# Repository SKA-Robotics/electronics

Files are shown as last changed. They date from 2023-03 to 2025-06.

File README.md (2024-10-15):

# Electronics
This repository contains documentation of electronic modules used on Sirius 2 Rover.

## How to use this repository
First, clone this repository to your computer.

```bash
$ git clone https://github.com/SKA-Robotics/electronics
```
Open ``SKAR.DsnWrk`` file in Altium designer.
This will load every project into your workspace, allowing you to browse or edit any of them.
When adding a new project, make sure it's part of the project group.

## Maintaining clean and readable documentation

To ensure that everyone can read the documentation, include following files in the final release:
- Datasheets of all important components used
- Any custom libraries containing schematic and layout files
- Schematic **in *.PDF* format**
- Manufacturing data (X2 gerbers)
- Exported 3D model in *.step* format (make sure your stackup has correct thickness set!)
- Images or 3D renders of the both sides
- A short README with description of your board, functionalities, connectors and instructions

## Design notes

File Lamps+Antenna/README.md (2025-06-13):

## Short description
This board contains three parts:
- 24V Step-Up/Step-Down voltage regulator
- LED signal tower controller
- POE injector

## Schematic
The full schematic is available at [schematic.pdf](schematic.pdf)

## Pcb layout
Board dimensions: 100m x 80mm

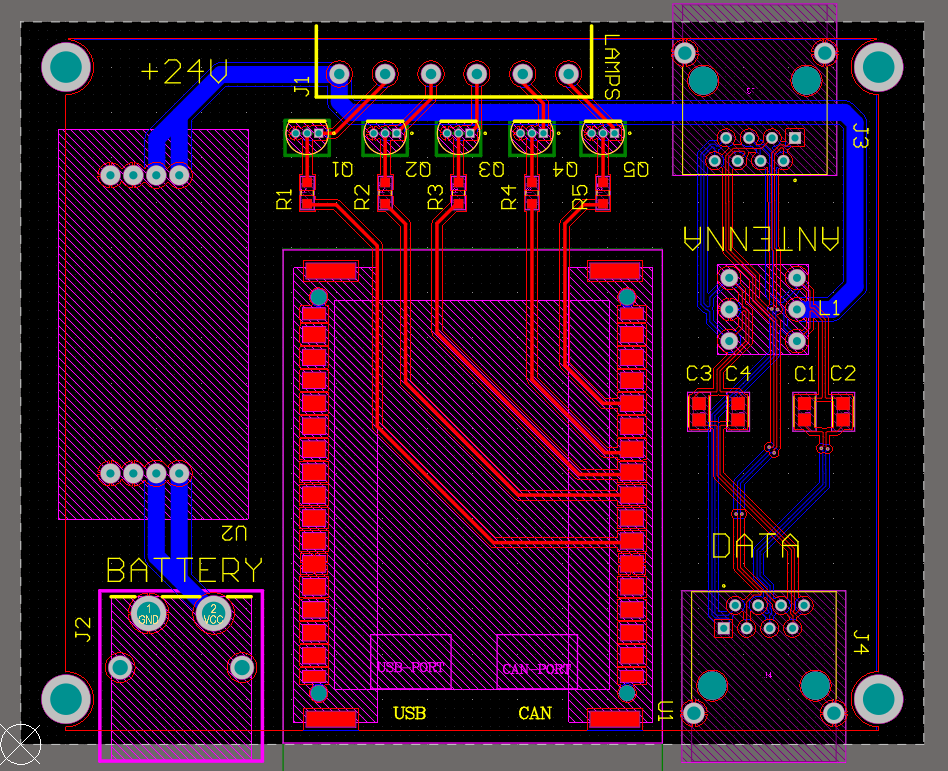
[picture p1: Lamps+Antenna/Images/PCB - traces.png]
PCBTraces


### 3D view
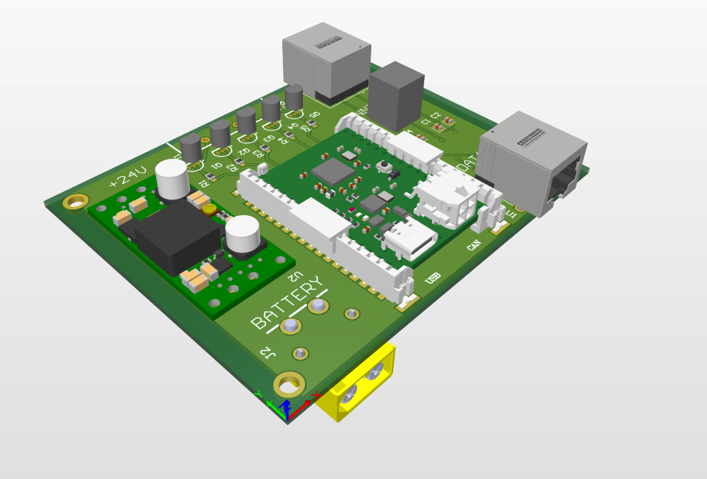
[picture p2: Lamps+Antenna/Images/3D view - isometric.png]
Isometric

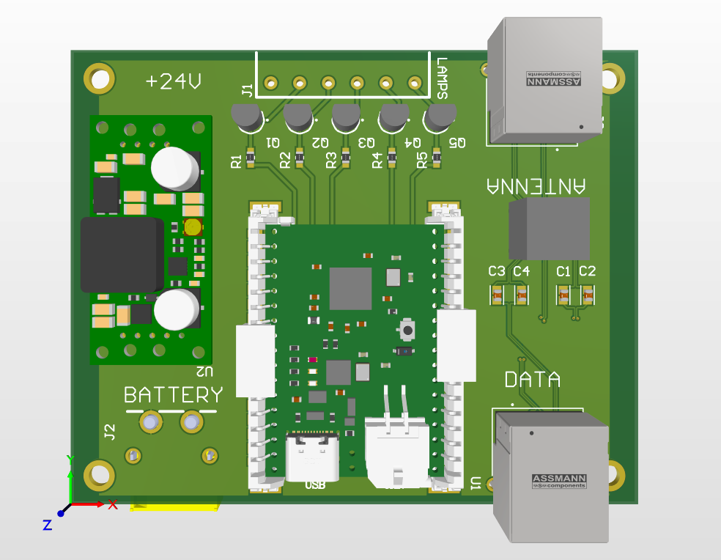
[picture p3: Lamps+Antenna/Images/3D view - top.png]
Top

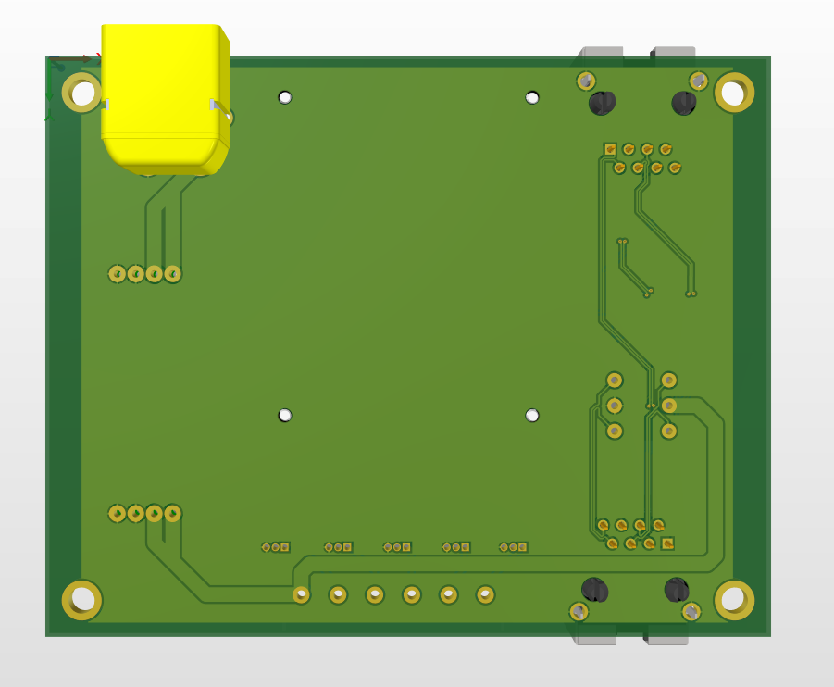
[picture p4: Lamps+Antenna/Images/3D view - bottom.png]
Bottom

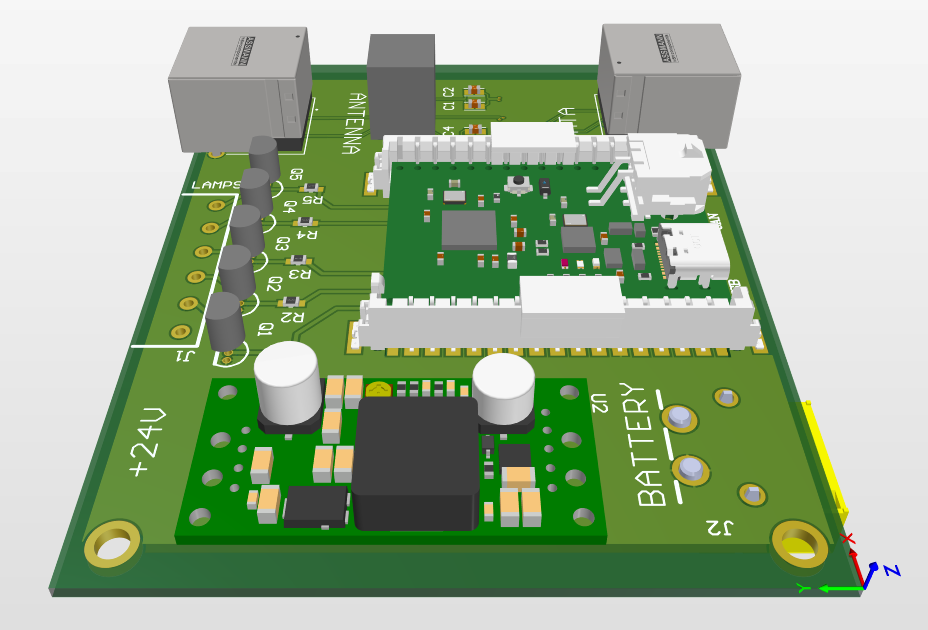
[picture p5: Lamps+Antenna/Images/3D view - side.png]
Side


### Components list
- [CANduino](https://github.com/SKA-Robotics/electronics/tree/main/CANduino)
- [Pololu 24V Step-Up/Step-Down Voltage Regulator](https://www.pololu.com/product/2582)
- [Transistor BC546B](https://www.tme.eu/pl/details/bc546b-dio/tranzystory-npn-tht/diotec-semiconductor/bc546b/)
- [Transformator unsoldered from MikroTik POE injector](https://mikrotik.com/product/RBGPOE)
> In transformator pins 1-2 and 5-6 should be switched respectively before soldering

# Inputs & Outputs

Inputs
-

|Name|Connector|Note|
|-  |- |-  |
|Power|XT60PW-M|The power connector should be soldered on a different side of the PCB than the rest of the components / voltage 3 V – 30 V (tested 21-29V)|
|CAN|Molex Micro-Fit 3.0|[SKAR CAN connector standard](https://github.com/SKA-Robotics/electronics/tree/main/Manipulator%20Harness#4-pin-connector)|
|USB|USB-C|Used only for CANduino programming and debugging|
|DATA|RJ-45|Data input for antenna ${\color{red}DO\quad NOT\quad CONNECT\quad TO\quad POE}$|

Outputs
-

|Name|Connector|Note|
|-  |- |-  |
|Lamps|Phoenix 6pins female|Open-collector output for LED signal tower|
|POE|RJ-45|POE output for antenna / 24 V ${\color{red}DO\quad NOT\quad CONNECT\quad TO\quad NON-POE}$|

# Lamps controller - Arduino code
[Arduino code for contolling lamps](lamps.ino)

# Credits
Designed by Selim Mucharski in 2025.

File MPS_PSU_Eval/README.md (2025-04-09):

# MPS PD power supply evaluation board
This is an evaluation board for MPS power delivery supply for main computer

# Overview
This board uses *MP5031* as a PD controller and *MP2491* as a step-down converter. Input voltage range is between 4-32V, and top power is 100W.
To achieve 100W PD, an external microcontroller with I2C is needed to set the registers.
The main goal of this board is to evaluate its performance as a power supply replacement, with higher stability and higher working temperature.
Components are placed on one side only, making the other side suitable for radiator placement.

# Pinout
This board uses XT60 as input and USB C as output, with additional 6 pin header for I2C and other controls.

# Pictures
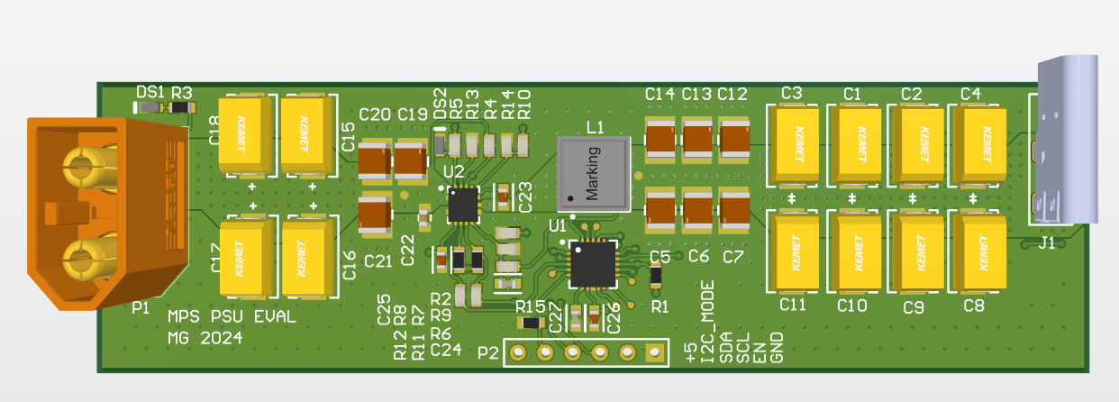
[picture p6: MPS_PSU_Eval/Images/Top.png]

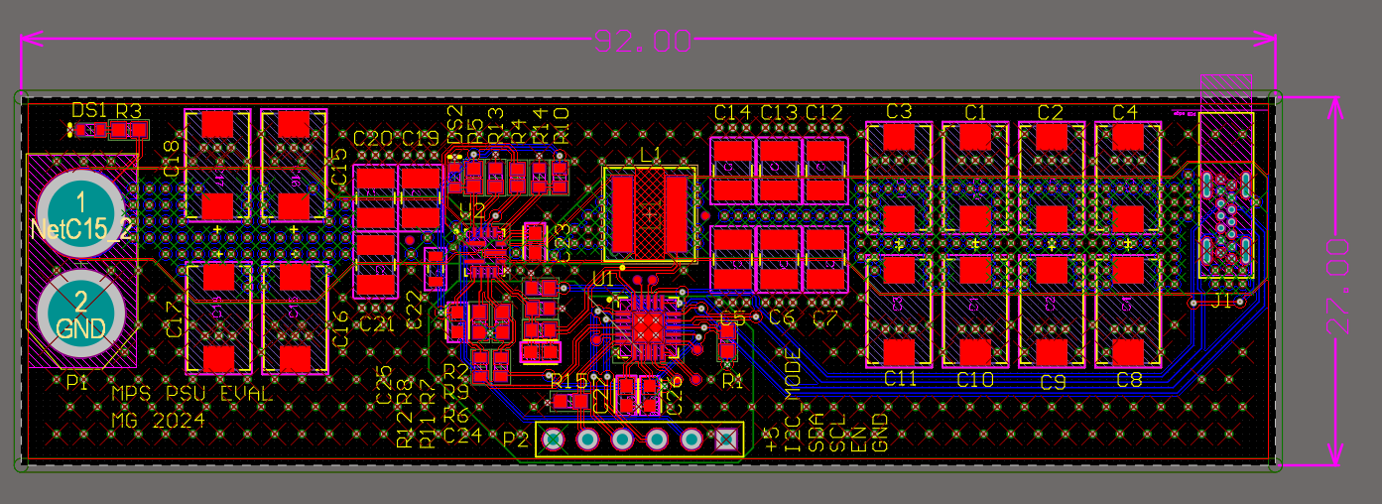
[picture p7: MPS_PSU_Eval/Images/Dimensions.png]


# Settings
To enable operations, following values have to be set in the registers:

0x08: 0xFFFF    -   set max current for PDO 4

0x0B: 0x8500    -   GPIO behaviour    

0x0D: 0x3490    -   GPIO behaviour

0x0E: 0xC898    -   GPIO behaviour

0x0F: 0x6464    -   Max power set to 100W

# Test results

## Simulations
DC IR analysis was conducted to determine current density in this design. The results are shown below

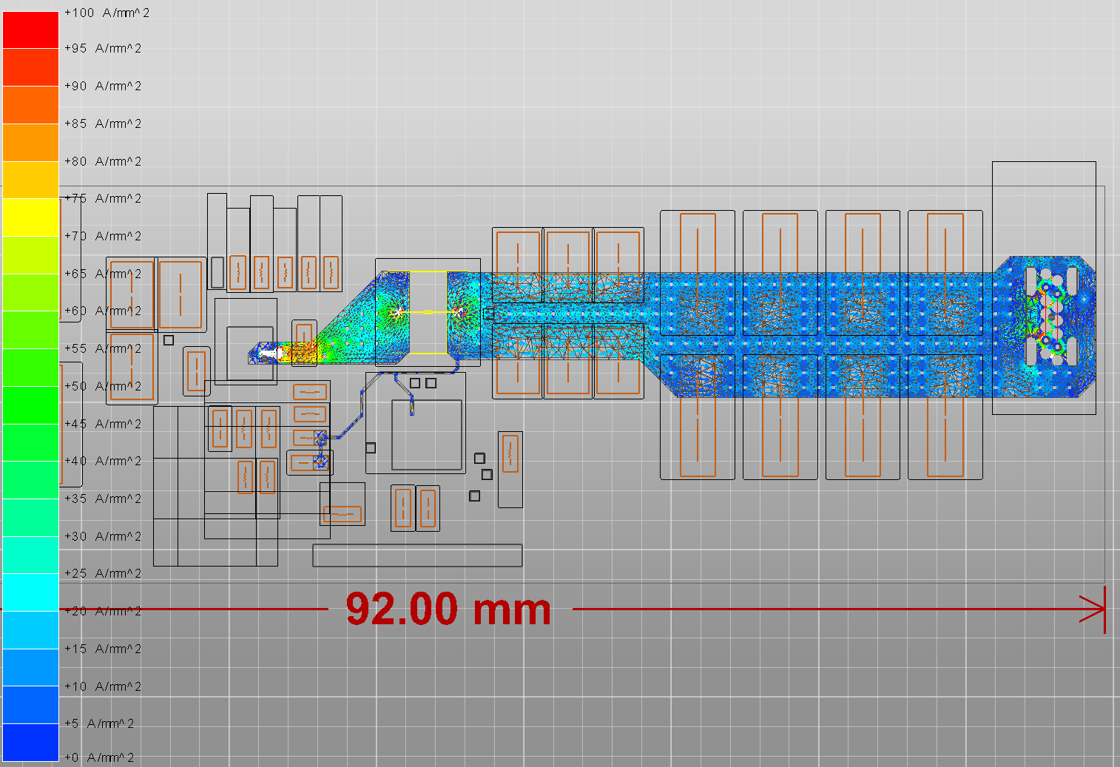
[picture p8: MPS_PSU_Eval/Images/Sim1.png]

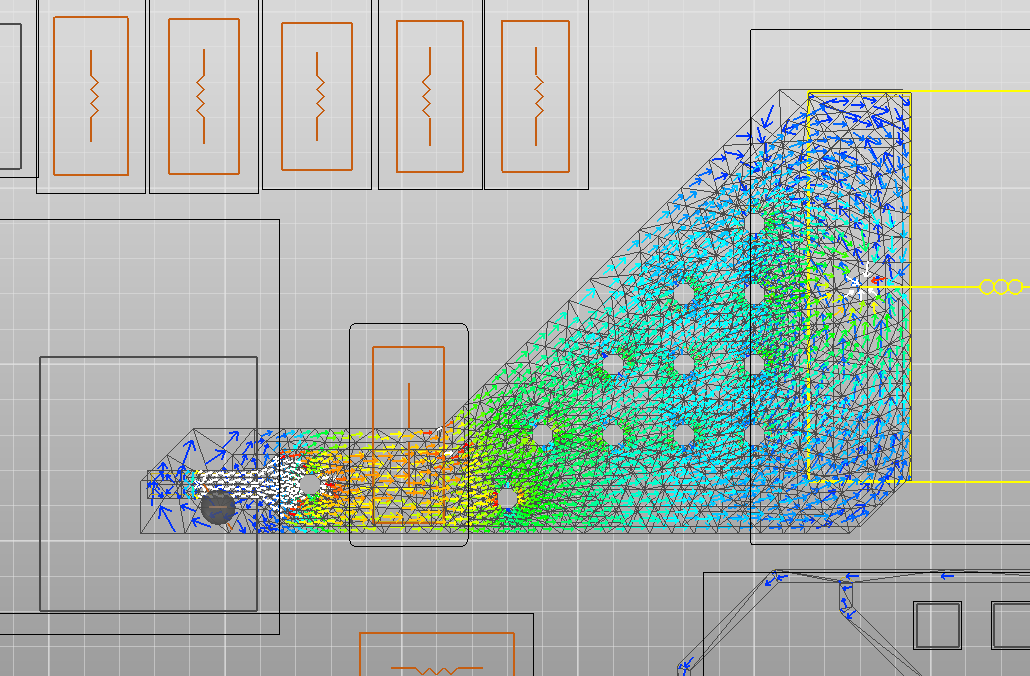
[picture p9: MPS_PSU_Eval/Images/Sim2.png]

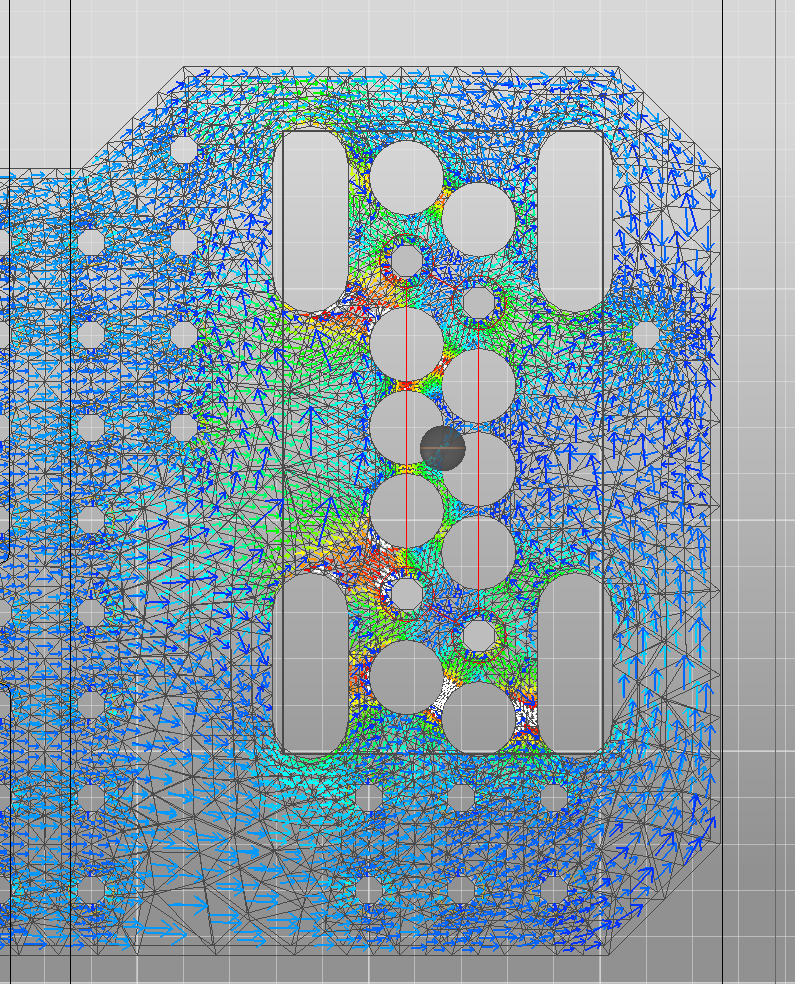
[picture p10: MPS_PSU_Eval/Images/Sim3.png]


Additional improvements can be made in converter output area by removing restricting via and adding another one to the left of output, to allow for another path for current to flow.
Another area for improvement is directly near USB C output, by tweaking clearance settings.

## Transient response

Device was tested for transient response from 0,5A to 3,5A at 20V output.
Slew rate was 0.5A/us and 1A/us. Scope was located directly at the load.
No real difference in transient response was observed.


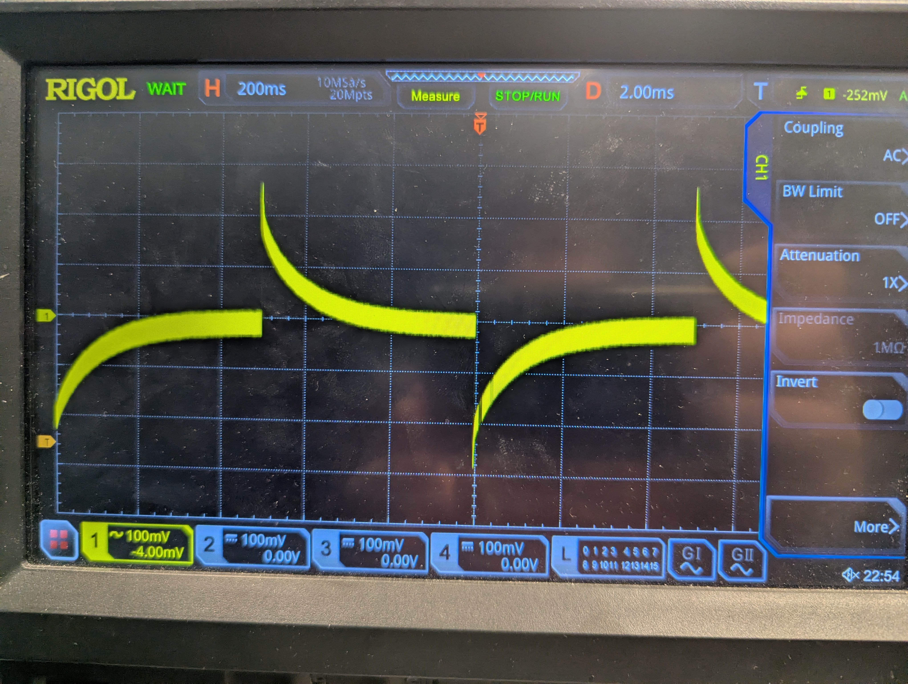
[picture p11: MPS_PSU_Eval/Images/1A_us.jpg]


## Thermals 

Temperature of the device was measured using IR camera.
The biggest hotspots are the converter IC and coil.
Current draw was ~3,5A.
Possible improvements are using a coil with lower ESR and adding a heat spreader for converter IC.
Proper operation was tested for over 120C
Pictured below is thermal image of the device with and without heatsink.

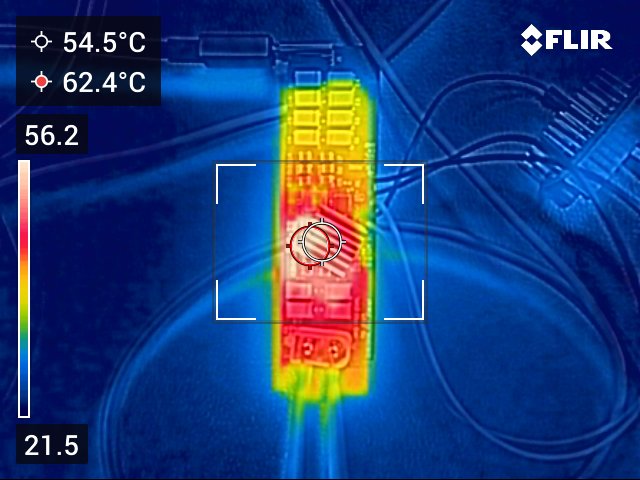
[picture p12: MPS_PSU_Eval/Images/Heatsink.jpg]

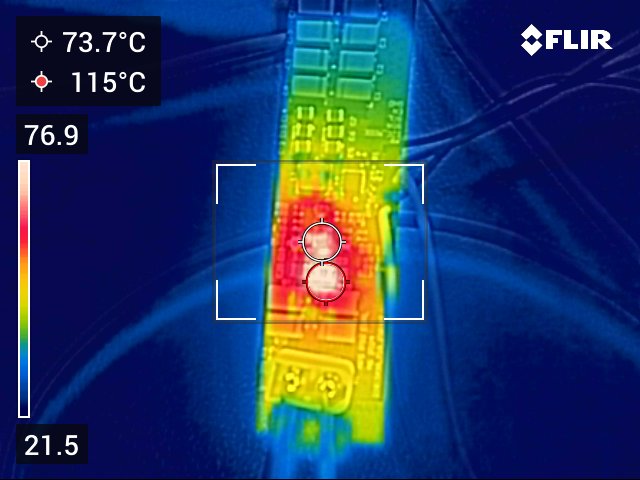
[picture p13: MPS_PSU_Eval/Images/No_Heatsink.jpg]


## Testing in the field

Device was used to power the rovers' PC for over an hour with no heatsing, while the PC was using max power with lots of transient loads.
There were no issues detected.

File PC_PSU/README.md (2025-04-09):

# PC Power supply
This is Power Delivery compatible PC power supply.

# Overview
This board uses *MP5031* as a PD controller and *MP2491* as a step-down converter. Input voltage range is between 4-32V, and top power is 100W.
To cool power path, a Raspberry Pi active cooler is used.
Atmega32u4 is used as a main microcontroller that monitors operation and sets correct register values for *MP5031* to enable 100W PD.
Spare GPIO  from *MP5031* are connected to MCU to allow further monitoring.
Additional functions realised by Atmega32u4 are: Fan control and speed monitoring, RGB button driving, internal temperature monitoring (NTC), external temperature monitoring (DS18B20) and output voltage sensing.

5V is supplied from either internal LDO or PC USB port. To prevent backdriving, ideal diodes are used in parallel for each source.
Active source is displayed using additional LEDs.
Moreover, *Voltage in* and *Power Good* are also connected to external LEDs.

There are 2 vertical USB ports, one for power and other for PC communication.
Extra filtering is added to avoid ESD damage (designed for 8kV/15kV IEC Contact/Air Discharge).

# Pinout
## RGB
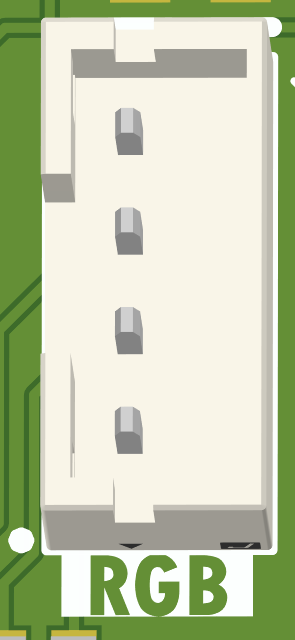
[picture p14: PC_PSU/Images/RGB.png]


LED1

LED2

LED3

+5V

## TEMP

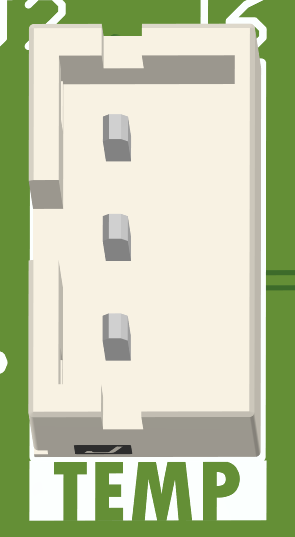
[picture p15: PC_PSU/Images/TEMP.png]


GND

DQ

+5V

## FAN

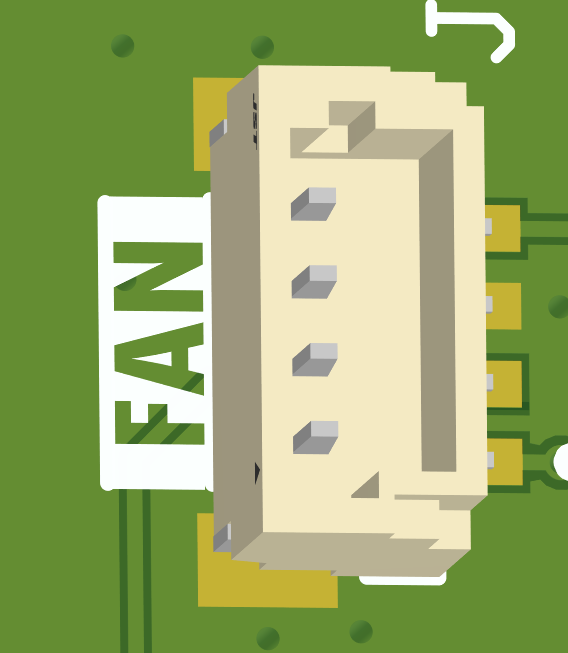
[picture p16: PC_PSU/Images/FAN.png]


Tach

GND

PWM

+5V

# Pictures
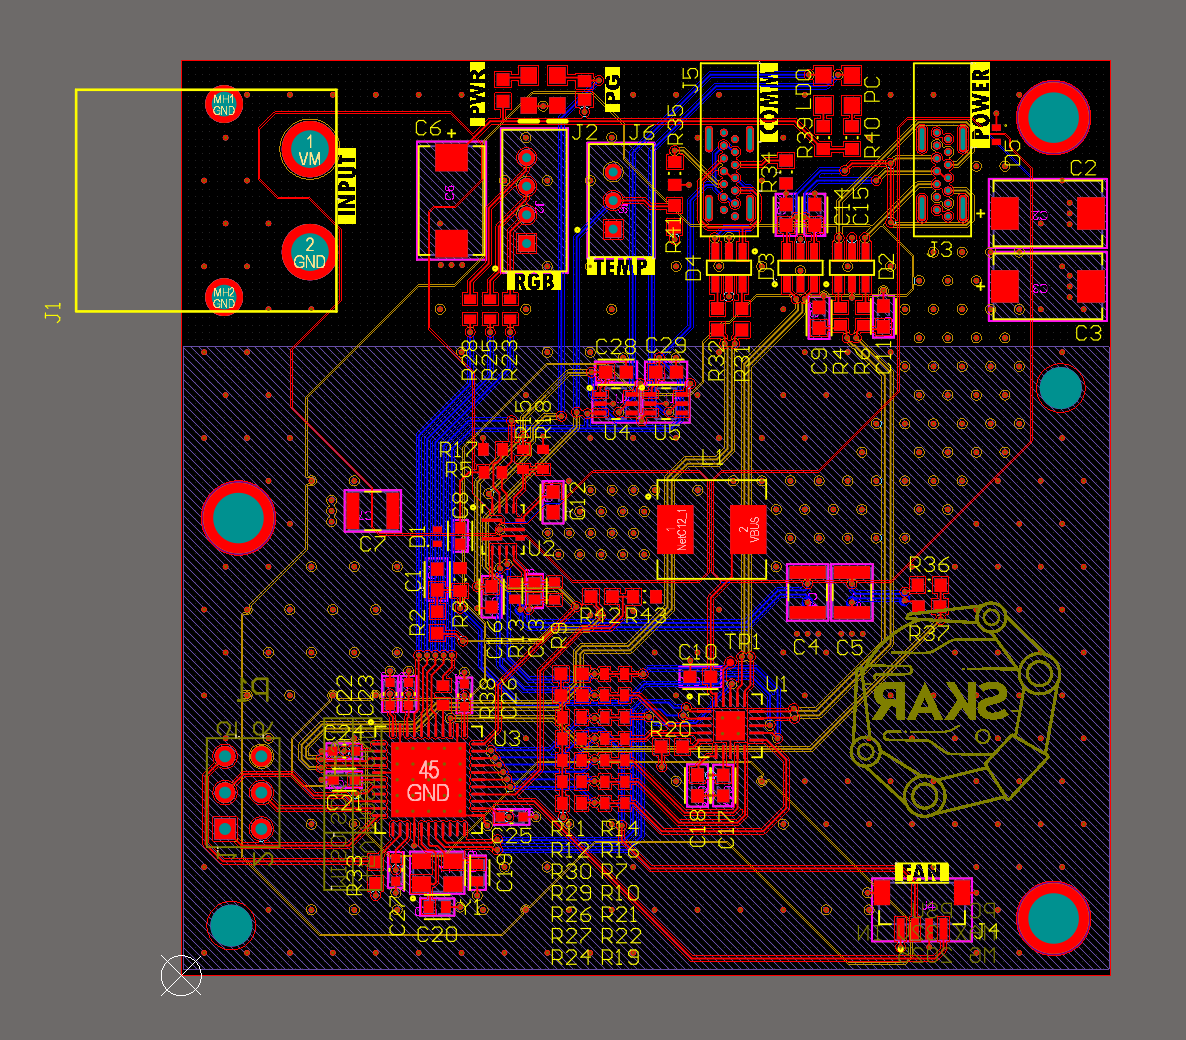
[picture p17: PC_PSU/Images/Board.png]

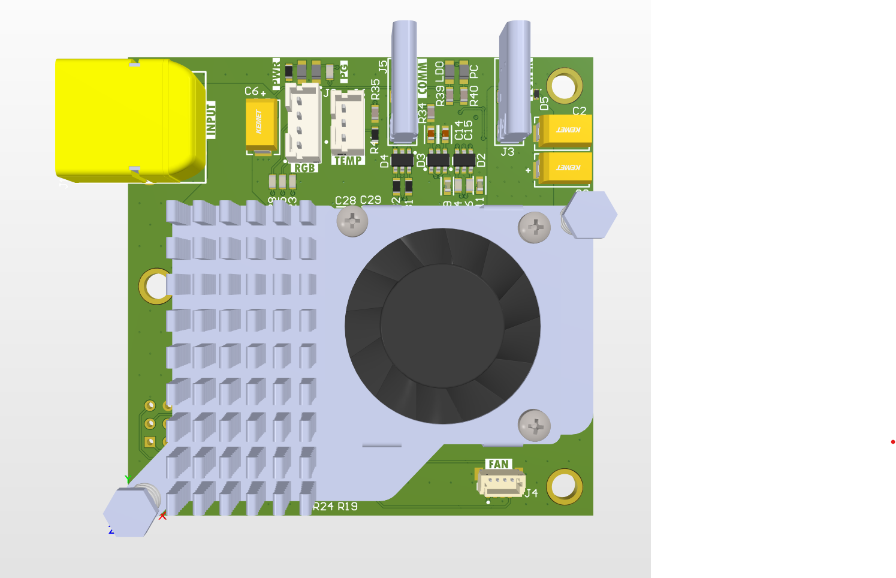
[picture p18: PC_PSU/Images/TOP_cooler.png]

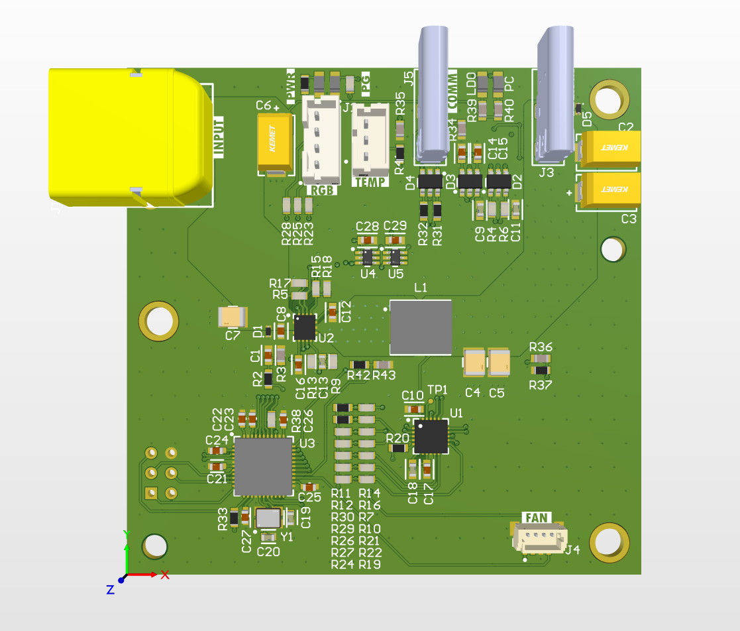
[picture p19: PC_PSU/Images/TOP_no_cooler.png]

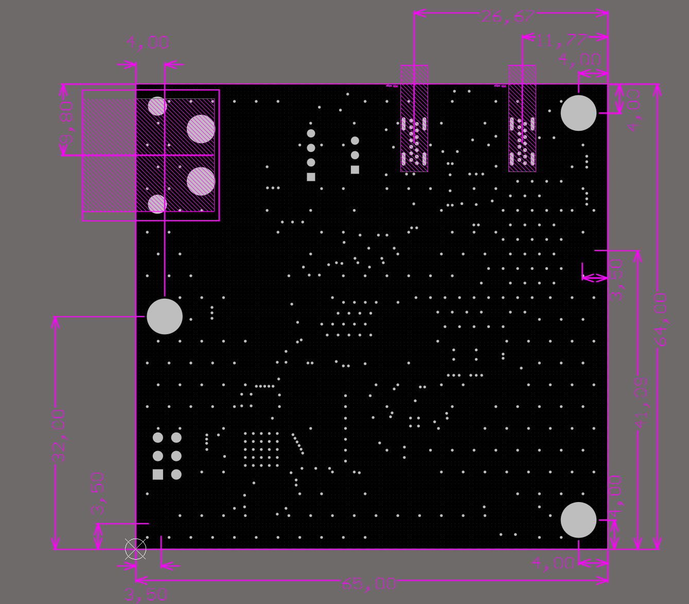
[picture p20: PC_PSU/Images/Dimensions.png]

# Notes
2 devices (to be) made, one as a spare. Source code can be found here (TBD)

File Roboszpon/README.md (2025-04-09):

# Roboszpon DC motor driver
This is a custom DC motor driver made to replace previous solution

# Overview

This board uses *STM32F103* as a main MCU and dual *DRV8873* to drive DC motors with up to 6.5A continous current.
Additional connectors for SPI encoders allow for closed loop control.
CAN is used for communication with other devices.
There is additional unused UART header for debugging.
Motor drivers feature a current monitoring output, connected to internal ADC of STM32 MCU.
3.3V for STM32 is provided by onboard LDO connected to 5V from CAN connector.
4 LEDs are added as a current device state indicator.
These are mounted sideways, to allow for them to stick out of the enclosure.
Input is protected by a 10A fuse and TVS diode.
# Pinout
This board uses all PTSM connectors, to be used inside a box enclosure.
## CAN
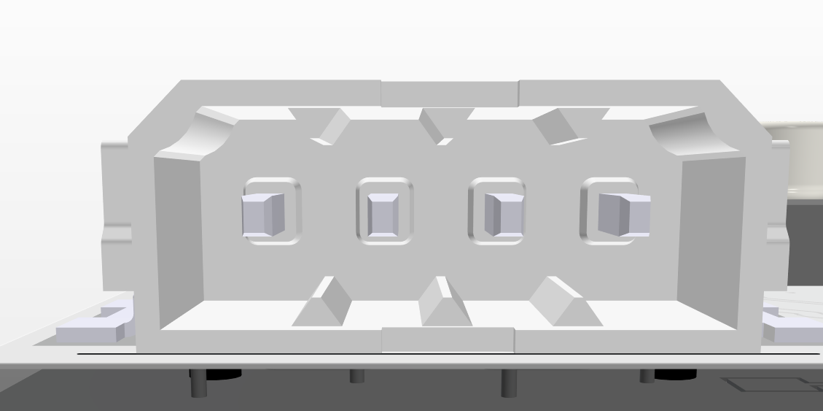
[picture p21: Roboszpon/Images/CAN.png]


GND, CANL, CANH, +5V

## Encoder

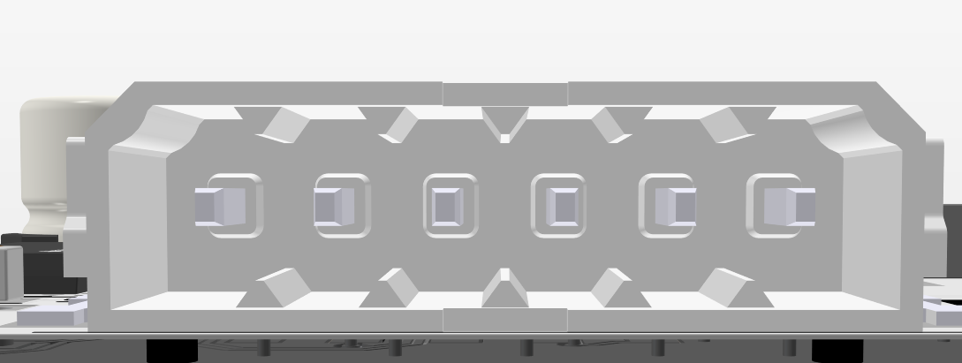
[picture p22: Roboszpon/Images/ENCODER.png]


GND, +3.3V, MISO, MOSI, SCK, CS

# Pictures
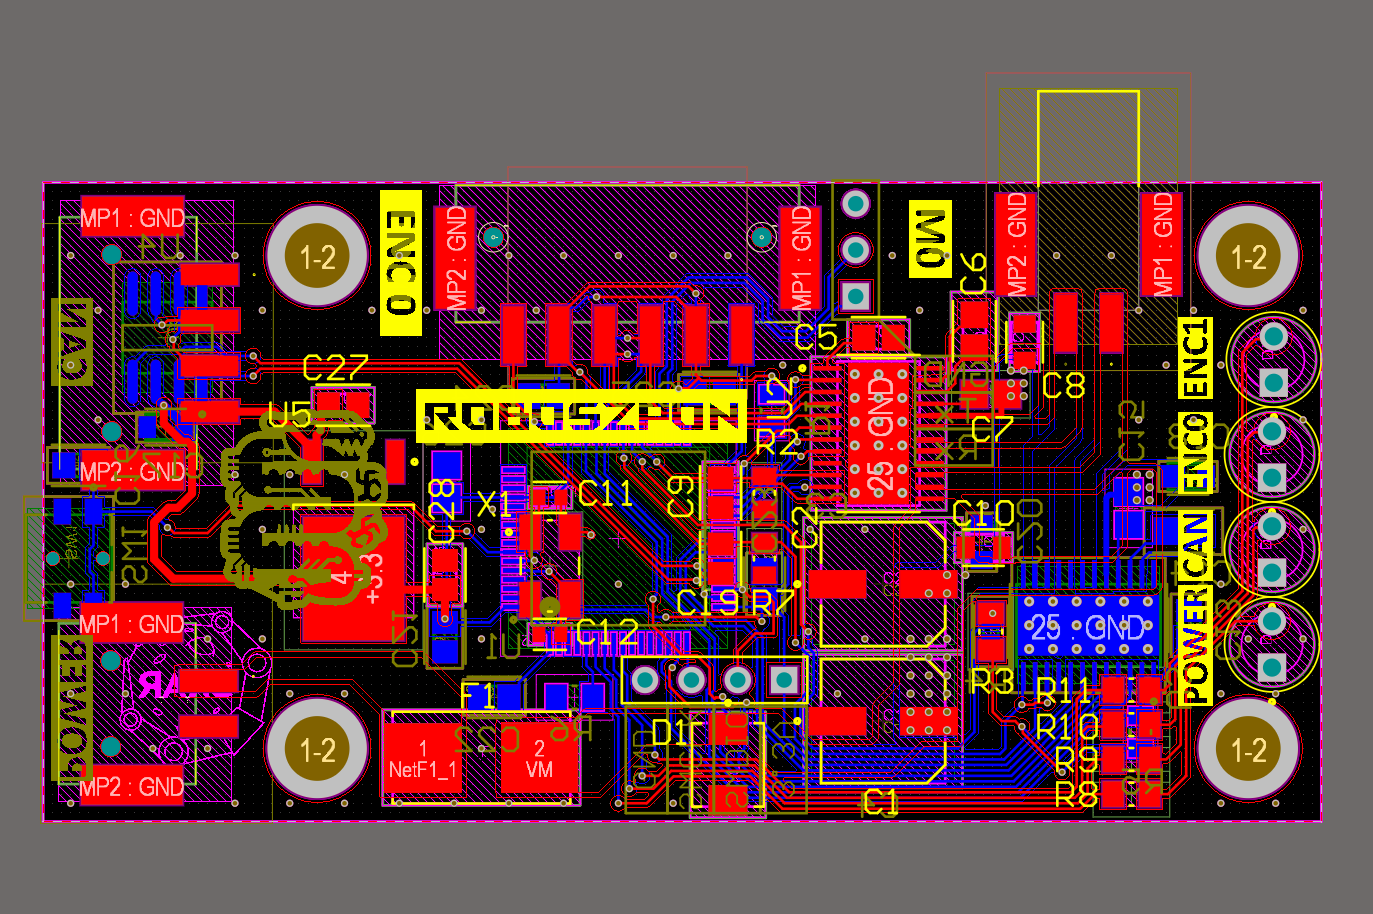
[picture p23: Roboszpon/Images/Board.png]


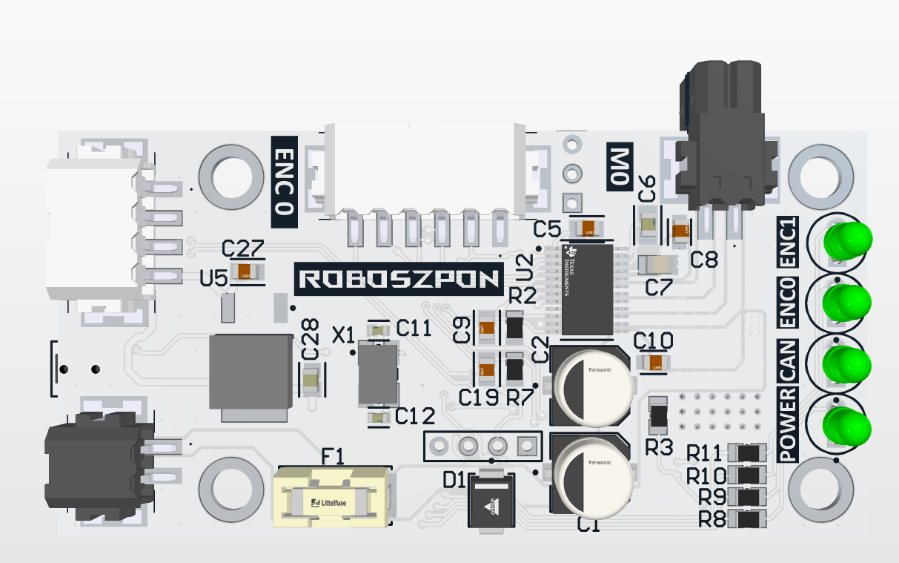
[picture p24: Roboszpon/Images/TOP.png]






# Notes

A total of 10 units were made

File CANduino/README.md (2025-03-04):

# CANduino
## Short description
CANduino is a Arduino Micro-like board capable of communicating via the CAN 2.0 bus. It is based on ATmega32u4 microcontroller.

[ATmega32u4-documentation](https://ww1.microchip.com/downloads/en/devicedoc/atmel-7766-8-bit-avr-atmega16u4-32u4_datasheet.pdf)

## Schematic
The full schematic is available at [Images/schematic.pdf](Images/schematic.pdf)

## Pcb layout
Board dimensions: 43mm x 30.5mm  
Height: 0.63mm (board) + 10.29mm (Micro-Fit) = 10,92mm (total)

PCBTraces

### 3D view
Isometric
Top
Bottom
Side

### Pinout
|Pin No.|Pin name|Pin No.|Pin name|
|-  |- |-  |-  |
|1  |+5 |34 |GND|
|2  |MOSI |33 |+5|
|3  |SCK |32 |SS/17|
|4  |MISO |31 |+5|
|5  |RST |30 |7|
|6  |GND |29 |GND|
|7  |2 |28 |AREF|
|8  |.11 |27 |A5|
|9  |.3 |26 |A4|
|10 |0 |25 |A3|
|11 |1 |24 |A2|
|12 |TXLED  |23 |A1|
|13 |4 |22 |A0|
|14 |12 |21 |HBW|
|15 |.6 |20 |CSCAN D10|
|16 |8 |19 |.13|
|17 |.9 |18 |.5|

For more information about using pins in program see [here](#pins).

## LED description
There are 3 LEDs on board:
- ${\color{red}Red}$ - PWR (board is powered)
- ${\color{yellow}Yellow}$ - TX CAN (Transmits CAN data)
- ${\color{green}Green}$ - RX CAN (Receives CAN data)

LEDs

## Power supply
Board works on 5V.
Can be powered by USB-C port, CAN bus or 5V pin (better not at the same time)

## CAN bus
CANduino is using MCP2515 controller with MCP2544FD transceiver during CAN communication. MCP2515 implements the CAN specification, Version 2.0B.

CAN controller bitrate: 1 Mb/s

[MCP2515-documentation](https://ww1.microchip.com/downloads/aemDocuments/documents/APID/ProductDocuments/DataSheets/MCP2515-Family-Data-Sheet-DS20001801K.pdf)

[MCP2544FD-documentation](https://ww1.microchip.com/downloads/aemDocuments/documents/APID/ProductDocuments/DataSheets/MCP2542FD-MCP2542WFD-4WFD-Data-Sheet-DS20005514C.pdf)

### MicroFit pinout
Pinout is compatible with "Sirius 2 standard".
Check current standard here: [Repository](https://github.com/SKA-Robotics/electronics/blob/main/Manipulator%20Harness/README.md)

#### MicroFit pinout used in CANduino

MicroFit

|CAN_L|CAN_V|
|- |- |
| GND | +5V |

### 120 Ω resistor 
To terminate bus with a 120 Ω resistor connect two pins between Micro-Fit and USB-C port using jumper. 

## Programming
CANduino can be programmed using USB-C port.
Programming is the same as in Arduino.

### Pins 
Side pins enable to get access to most of ATmega pins.  
For more information about pin mapping read Arduino documentation: [link](https://docs.arduino.cc/retired/hacking/hardware/PinMapping32u4/)
#### Analog pins
Analog pins are marked with letter "A", e.g "A1".
#### Digital pins
Digital pins are marked with numbers, e.g "12".
#### PWM pins
PWM pins are marked with leading ".", e.g ".3".

### CAN module
To communicate via CAN bus you can use the Arduino CAN library. Full documentation:
[Repository](https://github.com/sandeepmistry/arduino-CAN)

Wiring in CANduino is traced as default.

| Microchip MCP2515 | ATmega32u4 (Arduino pin names) |
| :---: | :-----: |
| VCC | 5V |
| GND | GND |
| SCK | SCK |
| SO | MISO |
| SI | MOSI |
| CS | 10 |
| INT | 2 |

# Use CANduino in your project
To use CANduino in your project you can import [CANduinoLib](CANduinoLib/) library to your Altium Designer project.
Footprint is compatible with [299-017-299198-1 EDAC](https://www.tme.eu/pl/en/details/299-017-299198-1/board-to-board-connectors/edac/) connector.

# Credits
Designed by Selim Mucharski and Jakub Bawej.  
Graphic designer - Tomasz Żebrowski.  
Special thanks for Michał Gołąb and Adam Jeliński for support.

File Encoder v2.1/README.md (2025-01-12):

# Encoder 2.1
This is a second edition of a magnetic encoder PCB used for position feedback for wheel motors

# Overview
This board was designed using the MA732 14-bit magnetic encoder chip to measure incremental angular position for wheel motors with a help of a diametrically magnetized magnet.

Output is incremental position using ABZ pulses, connected to 6-pin Molex micro-fit

There's an option for 10k NTC thermistor to measure temperature next to the motor

Blue -> power present

Red -> magnet too close (MGH)

Yellow -> magnet too far (MGL)

# Pinout


| B | A | 5V |
| - | - | -  |
| Z |Rt |GND |

# Pictures



# Notes
5 units (to be) produced.
3V3 power is achieved using internal LDO (300mA max). This will hopefully avoid failure due to voltage spikes.

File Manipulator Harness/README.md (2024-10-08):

# Manipulator Harness
This is a wiring harness connecting Roboszpon box inside the frame with motors and encoders located on the manipulator, as well as 12V power for the gripper servo

# Overview
Wiring harness is designed with regular Molex Micro-Fit 3.0 connectors in mind.
Cable used is 20AWG or 0.5mm^2 silicone coated copper wire.
Connectors used:
8-pin for rotation, 12-pin for motors and servo power, 16-pin for encoders
6-pin for encoders, 2-pin vertical for motors and 2-pin horizontal for servo power

# Part numbers
Male connectors:
- 43020-0200
- 43045-0427
- 43045-0600
- 43020-0800
- 43020-1200
- 43020-1600

Female connectors
- 43025-0200
- 43025-0400
- 43025-0600
- 43025-0800
- 43025-1200
- 43025-1600

Terminals:
- 43030-0001
- 43031-0001

For crimp connectors, a 18 AWG crimp is used, although a 20AWG crimp could be used as well

# Detailed pinout
All pinouts described here are referencing **male** connectors (as in, what you're plugging the harness into)

This is the current motor nomenclature and assigned CAN_ID for reference
- M0 - 0x3 - Rotation
- M1 - 0x2 - Shoulder
- M2 - 0x7 - Elbow
- M3 - 0x6 - Wrist raise
- M4 - 0x5 - Wrist rotation lower
- M5 - 0x4 - Wrist rotation upper

## 4-pin Connector

|CAN_L|CAN_V|
|- |- |
| GND | +5V |

## 6-pin Connector

| CS |SCLK|3.3V|
|- |- |- |
|MOSI|MISO|GND |

## 8-pin Connector

|M0+| CS |SCK |3.3V|
|-  |- |- |- |
|M1-|MOSI|MISO|GND |

## 12-pin Connector

This connector is used for the motors ant to power the gripper servo
|M1-|M2-|M3-|M4-|M5-|GND |
|-  |-  |-  |-  |-  |- |
|M1+|M2+|M3+|M4+|M5+|+12V|

## 16-pin Connector

|3.3V|CS1_a|MISO_a|MOSI_a|SCK_a|CS2_a| CS_c |SCK_c |
|- |- |- |- |- |- |- |- |
|GND |CS1_b|MISO_b|MOSI_b|SCK_b|CS2_b|MOSI_c|MISO_c|
 
 CS pins correspond to following motors:
 - CS1_a - M5 (Wrist rotation upper)
 - CS2_a - M4 (Wrist rotation lower)
 - CS1_b - M3 (Wrist raise)
 - CS2_b - M2 (Elbow)
 - CS_c - M1 (Shoulder)
 
# Photos


A complete harness without connectors.



Wiring inside Roboszpon box.

# Notes
While mounting the harness, make sure to remember about leaving extra length for movement of the joints. Nominal manipulator rotation is 180 degrees in either direction. Other angles are subject to change.
Harness can be secured with velcro stripes or zip-ties. Make sure that there is no interference between moving parts of the frame and your chosen mounting points.

When servicing the harness, try to make the wires equal lengths to balance forces acting on the connector (in case of sudden gripper separation).

While crimping new connectors, remove only as much isolation as is needed. A proper crimp should grab both metal parts of the wire and a bit of the isolation. A proper crimp should resist significant pull force. When inserting a crimped wire into a plastic housing, push until you hear a satisfying *click*, and ensure the wire is secured by pulling on it.

For further information, refer to manufacturers' guidelines.

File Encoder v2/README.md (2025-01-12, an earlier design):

# Encoder
This is a second edition of a magnetic encoder PCB used for position feedback at every rotating joint

# Overview
This board was designed using the MA732 14-bit magnetic encoder chip to measure absolute angular position for every rotating joint with a help of a diametrically magnetized magnet.

Output is absolute position using SPI, connected to 6-pin Molex micro-fit

Blue -> power present

Red -> magnet too close (MGH)

Yellow -> magnet too far (MGL)

# Pinout


| CS |SCLK|3.3V|
|- |- |- |
|MOSI|MISO|GND |

# Pictures



# Notes
15 units produced, some came out faulty.
Possible cause is long wires and direct 3.3V connection, might be beneficial to replace it with 5V and LDO regulator.

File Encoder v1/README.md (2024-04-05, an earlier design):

# Encoder
This is a magnetic encoder PCB used for position feedback at every rotating joint

# Overview
This board was designed using the MA732 14-bit magnetic encoder chip to measure absolute angular position for every rotating joint with a help of a diametrically magnetized magnet.

I/O signals are turned into differential signals using SN65C116xE drivers/receivers connected to IDC 8 and IDC10 sockets. Power for MA732 is supplied through a 3.3v LDO voltage regulator.

There are two output modes, ABZ incremental and SPI, that can be switched by using P5 jumper.
Output of both signals is differential, to allow interchangeability with wheel motors and their encoders.

For SPI connection, `CS` pin is routed to a separate connector, to allow a daisy chain connection of up to 4 devices. In this configuration, Input connector of one device should be connected to an output connector of another. This does not work for incremental mode (for obvious reasons).

There are 3 LEDs that indicate current state of the encoder.

Blue -> power present

Red -> magnet too close (MGH)

Yellow -> magnet too far (MGL)

# Pinout

## Input and output


Ground is differentiated with a square pad.
Looking from the top of the connector the pinout for incremental mode is as follows:

|Z_N|B_N|A_N|GND|NC|
|---|---|---|---|--|
|Z_P|B_P|A_P|NC|+5V|

For SPI mode pinout is:

|MOSI_N|MISO_N|SCLK_N|GND|NC|
|---|---|---|---|--|
|MOSI_P|MISO_P|SCLK_P|NC|+5V|

## Chip select 

Only pins 1 and 2 are connected to the encoder, while the rest connects to `CS_OUT` connector, shifting to the right.

Pin 1 -> CS_N

pin 2  -> CS_P

# Pictures



# Notes
There were 12 units made in total. All of the work in incremental ABZ mode, however due to manufacturing issues only a few of them work in SPI mode.

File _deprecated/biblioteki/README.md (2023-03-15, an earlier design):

# electronics

Tu można dawać biblioteki schematów i footprintów, tak żeby poźniej nie musieć robić wszystkiego od nowa, albo grzebać w innych projektach

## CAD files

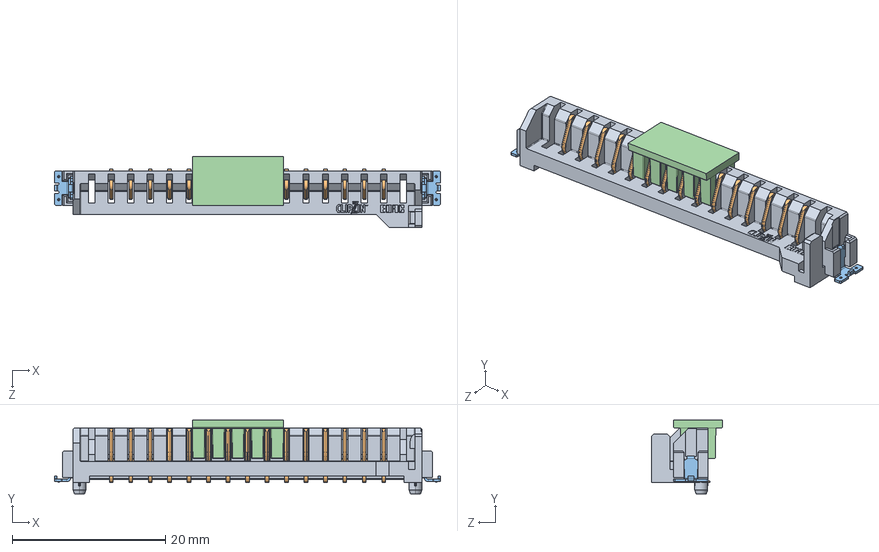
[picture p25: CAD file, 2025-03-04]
CANduino/CANduinoLib/299-017-299-198 - EDAC SMT Card Edge Connector.STEP
50.4 x 9.60 x 9.29 mm
299-210-017_20POS_with stabiliser

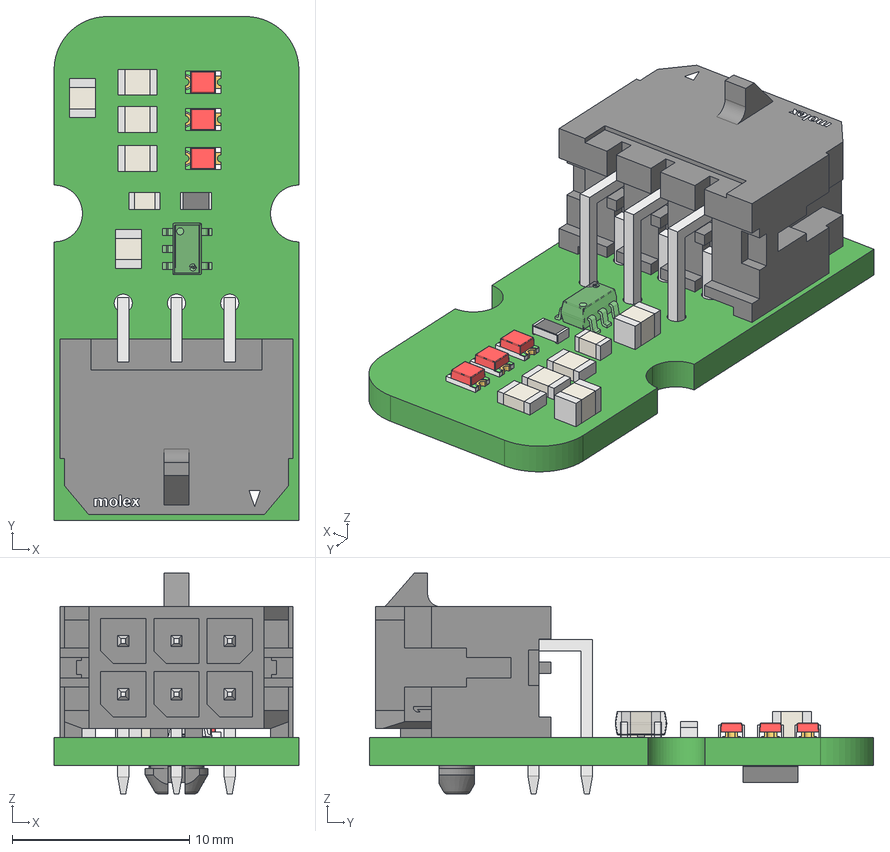
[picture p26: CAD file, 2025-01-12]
Encoder v2.1/Encoder_v2.1_3D_model.step
13.8 x 28.4 x 12.4 mm
IC_BODY
IC_LEG x 3
circle
IC_LEG_MIR1 x 2
Microchip logo
Extruded x 18
Mid_Body
Mark
Pins
New Marking
Molex Logo-LAPTOP-NQA1DCQ3
base x 3
cover x 3
housing x 3
marking x 6
base_2 x 3
Mark2 x 3

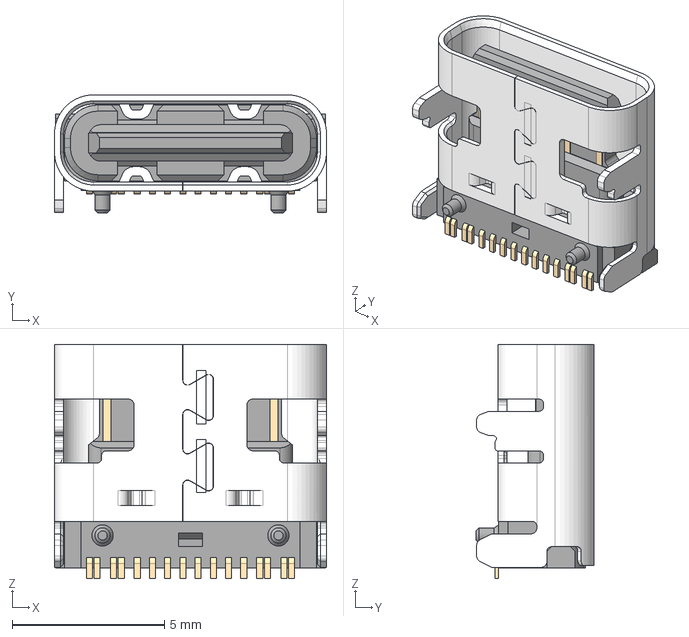
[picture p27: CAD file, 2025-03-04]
CANduino/3D models/USB4105-GF-A-060.stp
8.94 x 3.89 x 7.70 mm
USB4105-GF-A-060_PART1
USB4105-GF-A-060_PART2

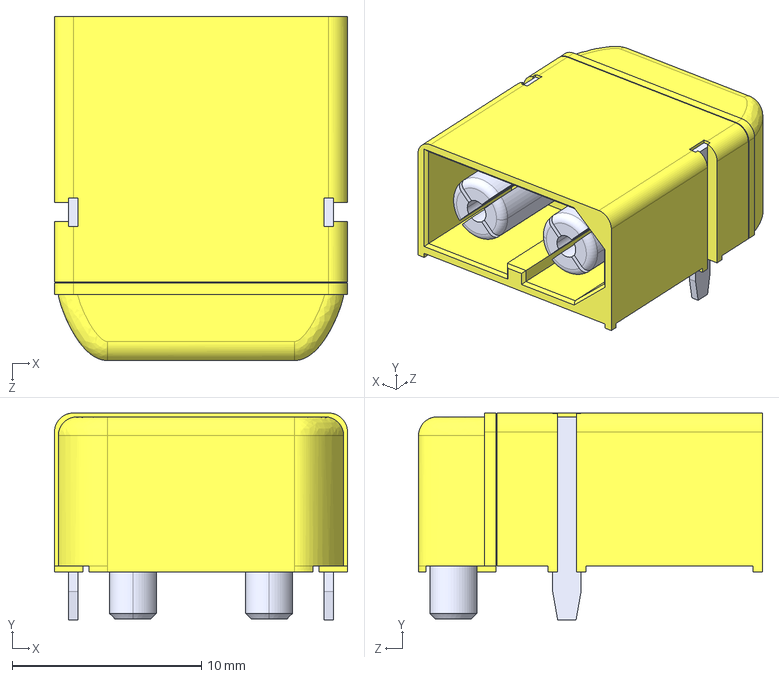
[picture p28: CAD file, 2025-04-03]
Lamps+Antenna/3D models/XT60PW-M--3DModel-STEP-269445.STEP
15.5 x 11.0 x 18.2 mm

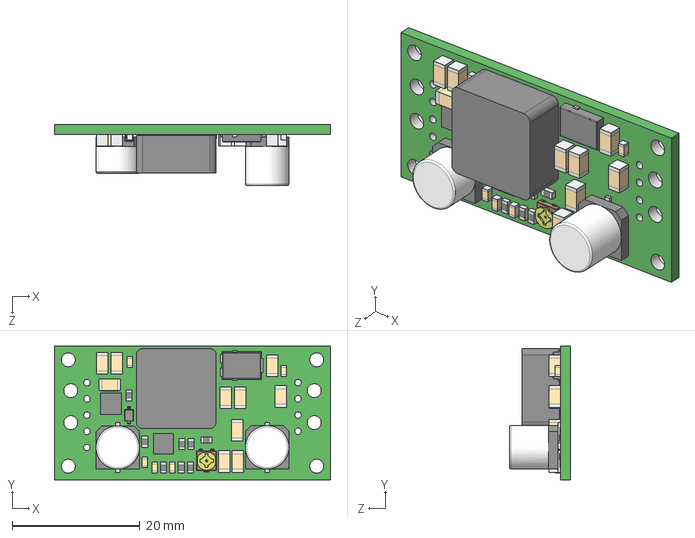
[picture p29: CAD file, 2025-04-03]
Lamps+Antenna/3D models/s18v20x-step-up-step-down-voltage-regulator.step
43.2 x 21.0 x 9.57 mm

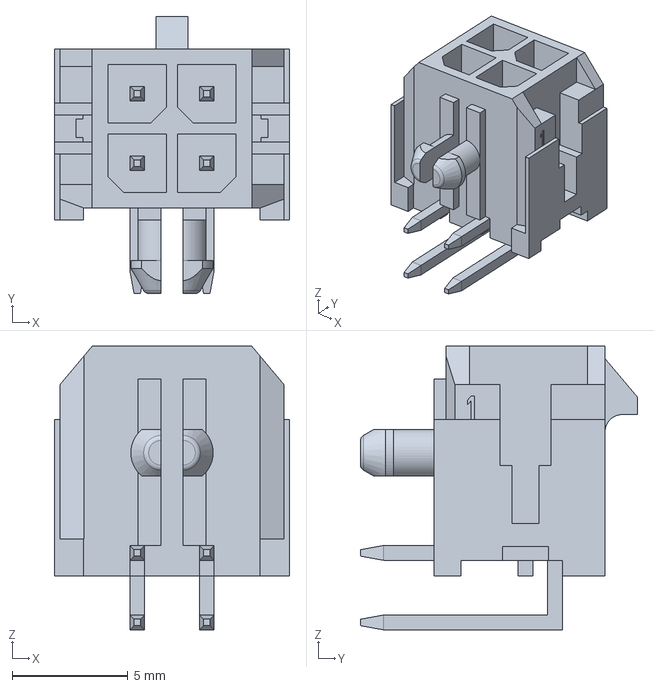
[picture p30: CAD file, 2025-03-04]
CANduino/3D models/43045-0400.stp
10.2 x 11.9 x 12.2 mm

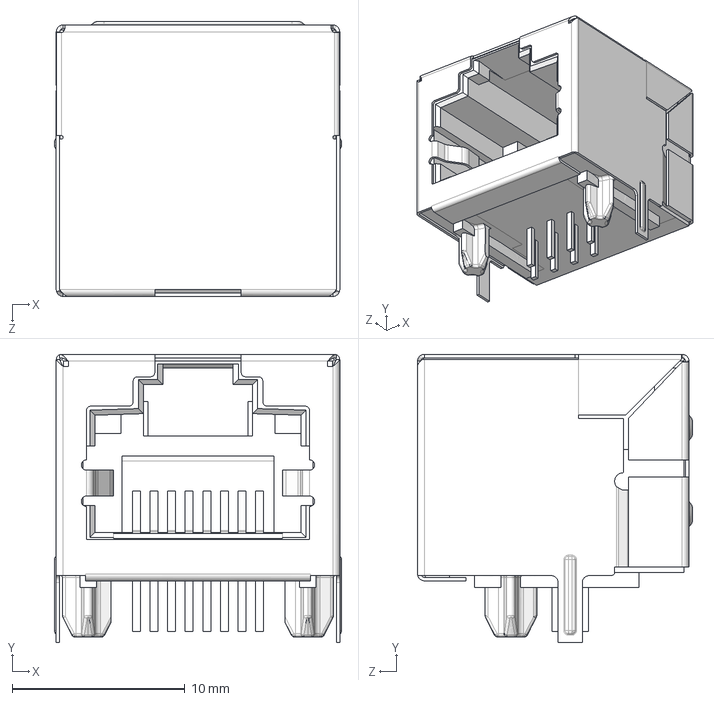
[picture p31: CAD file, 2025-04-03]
Lamps+Antenna/3D models/2501551-6.stp
16.6 x 16.7 x 15.9 mm

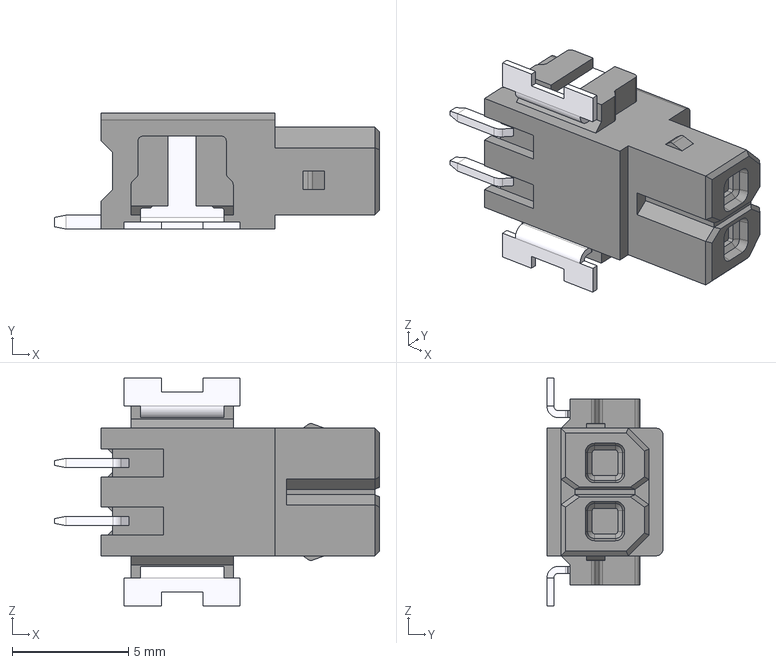
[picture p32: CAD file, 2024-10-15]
Roboszpon/Source/3D models/1815125.stp
14.0 x 5.00 x 9.80 mm

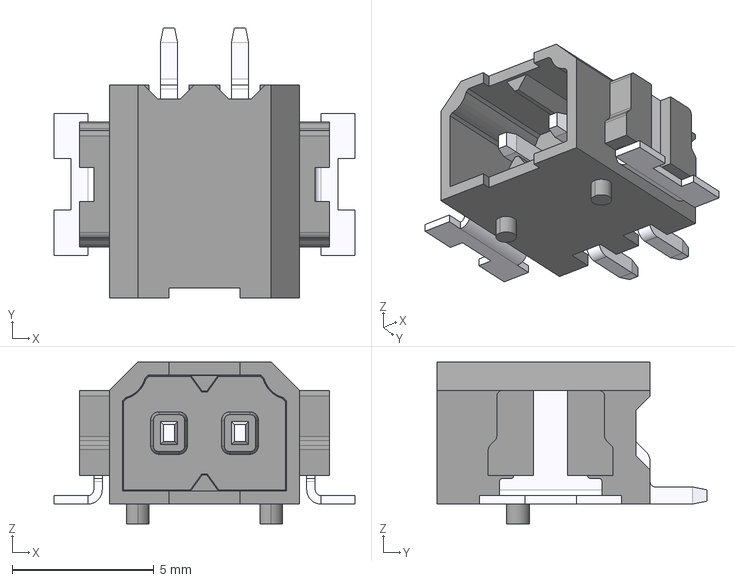
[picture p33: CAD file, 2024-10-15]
Roboszpon/Source/3D models/1708004.stp
10.6 x 9.50 x 5.70 mm

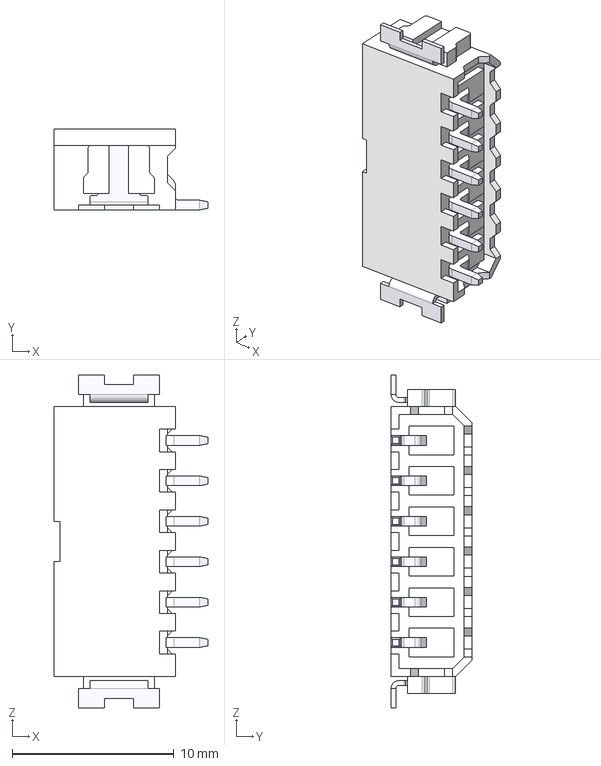
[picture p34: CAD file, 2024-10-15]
Roboszpon/Source/3D models/1814951.stp
9.50 x 5.00 x 20.6 mm

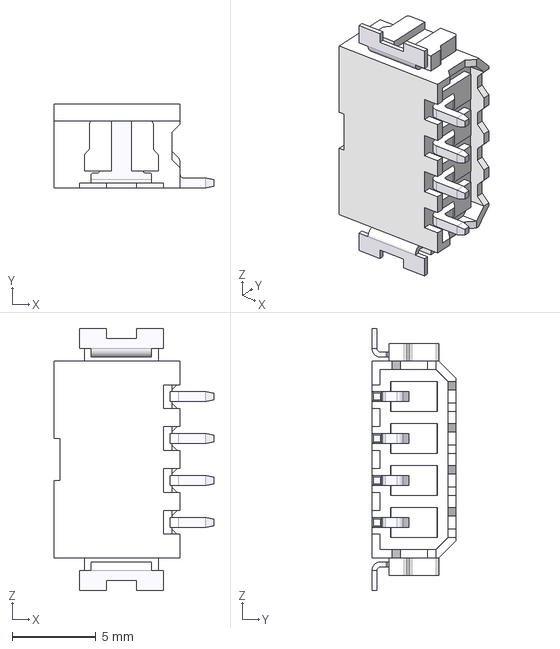
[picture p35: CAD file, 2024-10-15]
Roboszpon/Source/3D models/1814935.stp
9.50 x 5.00 x 15.6 mm

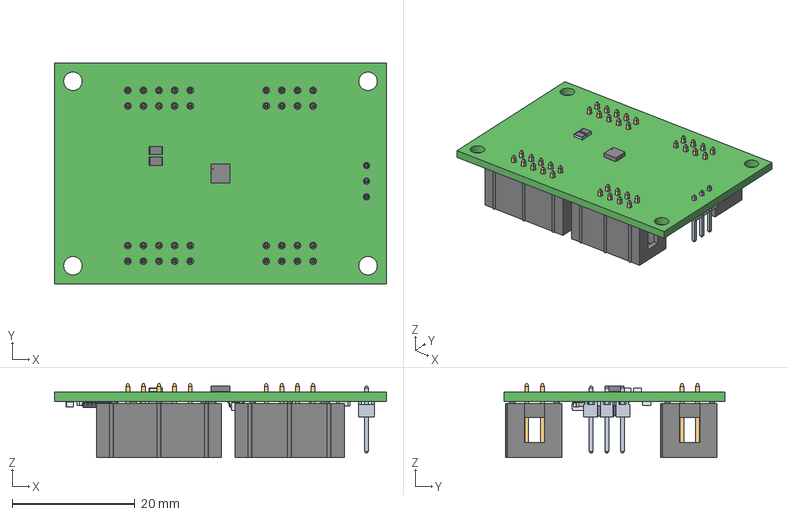
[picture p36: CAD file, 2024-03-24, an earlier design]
Encoder v1/Encoder_v1_3D_model.step
54.0 x 36.0 x 12.1 mm
6120xx21621_PIN x 36
Extruded x 22
TSW-103-07-X-S
base x 3
cover x 3
housing x 3
marking x 6
base_2 x 3
Mark2 x 3
Cap_KEMET_C0805C472J3HAC_eec x 9
IC_BODY
IC_LEG x 3
circle
IC_LEG_MIR1 x 2
Microchip logo
Mid_Body x 2
Mark x 2
BODY_MTC16
LEAD_MTC16 x 16

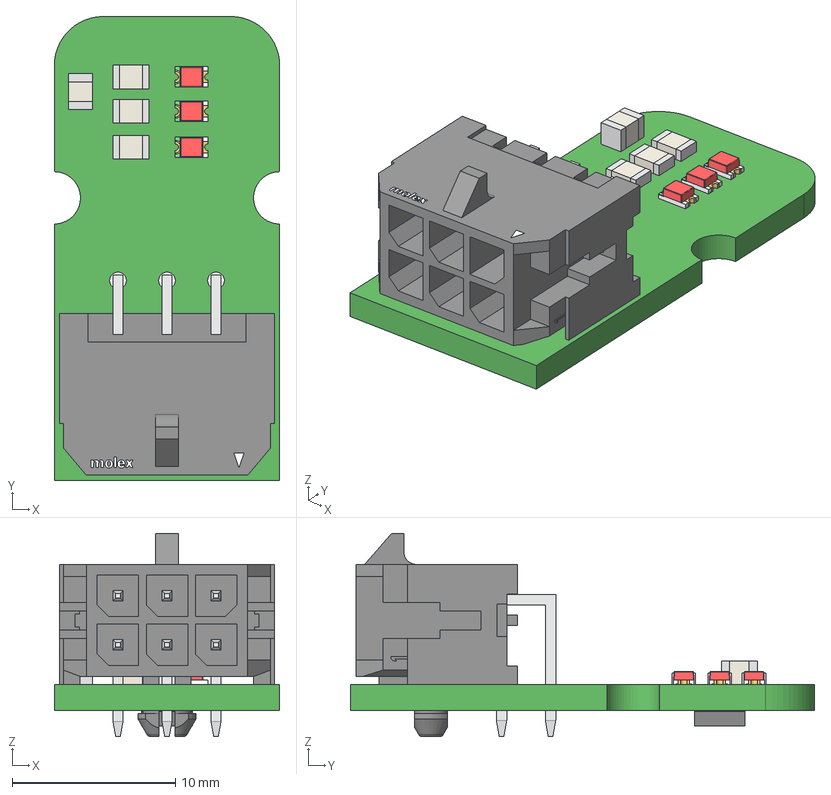
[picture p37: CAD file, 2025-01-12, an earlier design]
Encoder v2/Encoder_v2_3D_model.step
13.8 x 28.4 x 12.4 mm
Extruded x 12
Pins
New Marking
Molex Logo-LAPTOP-NQA1DCQ3
base x 3
cover x 3
housing x 3
marking x 6
base_2 x 3
Mark2 x 3

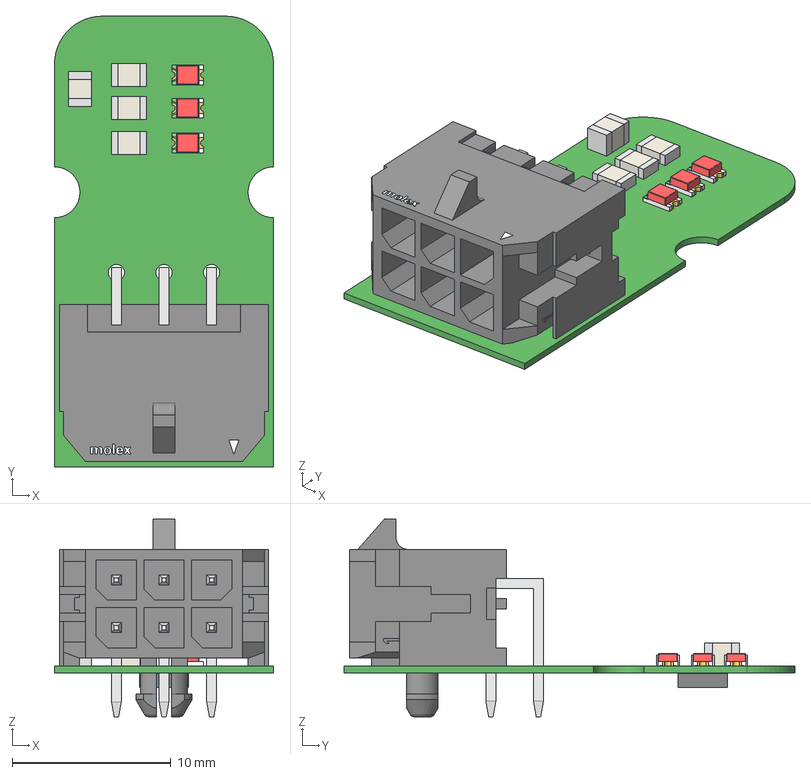
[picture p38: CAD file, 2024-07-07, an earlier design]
Encoder v2/enkoder2.step
13.8 x 28.4 x 12.4 mm
Extruded x 12
Pins
New Marking
Molex Logo-LAPTOP-NQA1DCQ3
base x 3
cover x 3
housing x 3
marking x 6
base_2 x 3
Mark2 x 3

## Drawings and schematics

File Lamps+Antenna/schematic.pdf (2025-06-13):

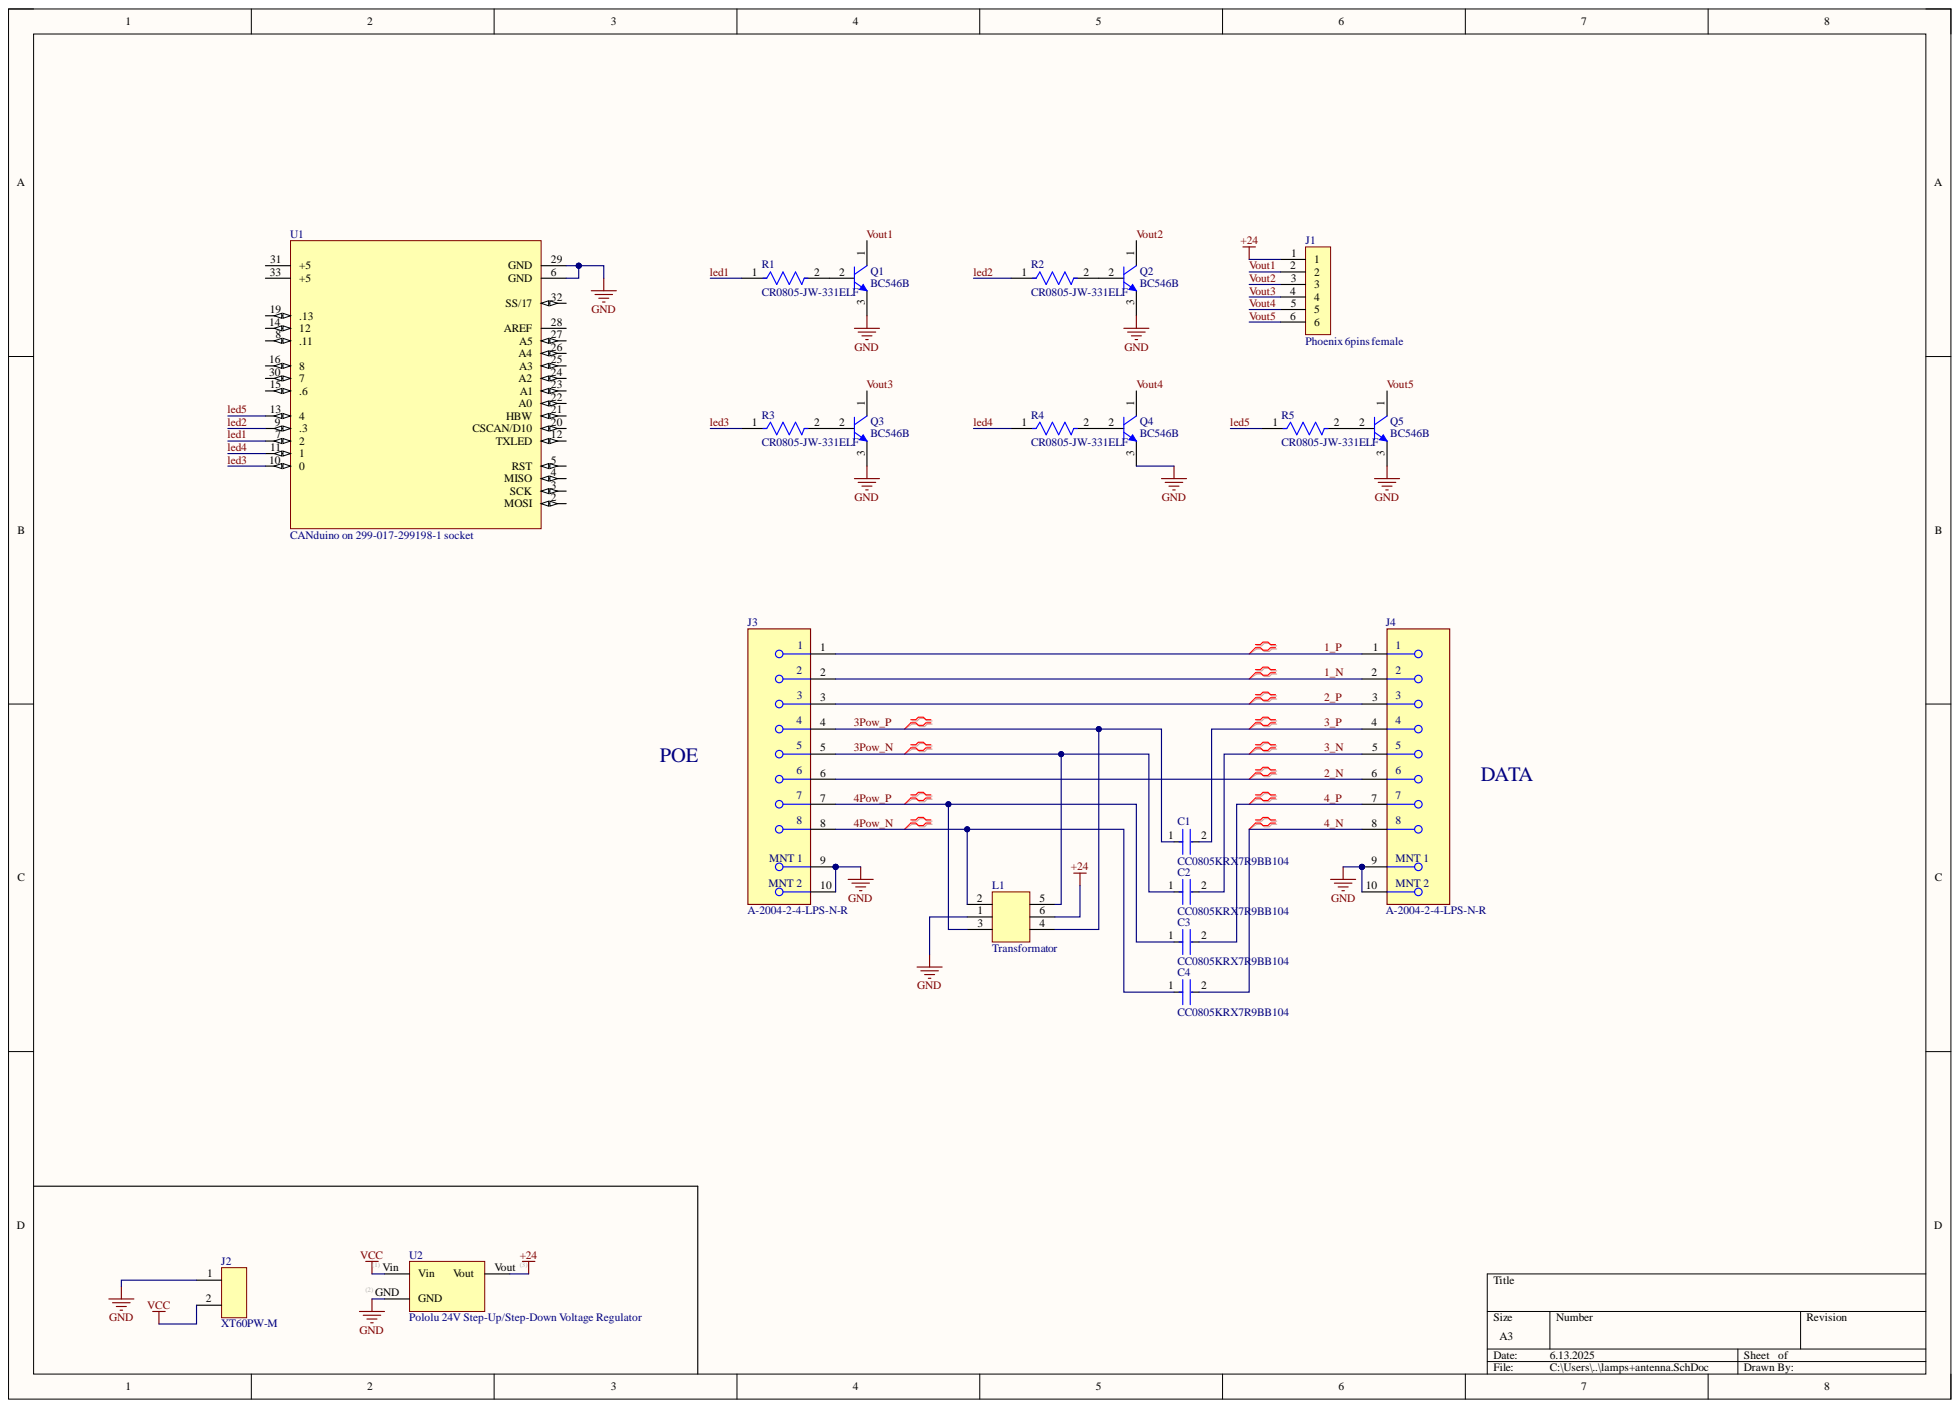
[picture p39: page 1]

Pololu 24V Step-Up/Step-Down Voltage Regulator

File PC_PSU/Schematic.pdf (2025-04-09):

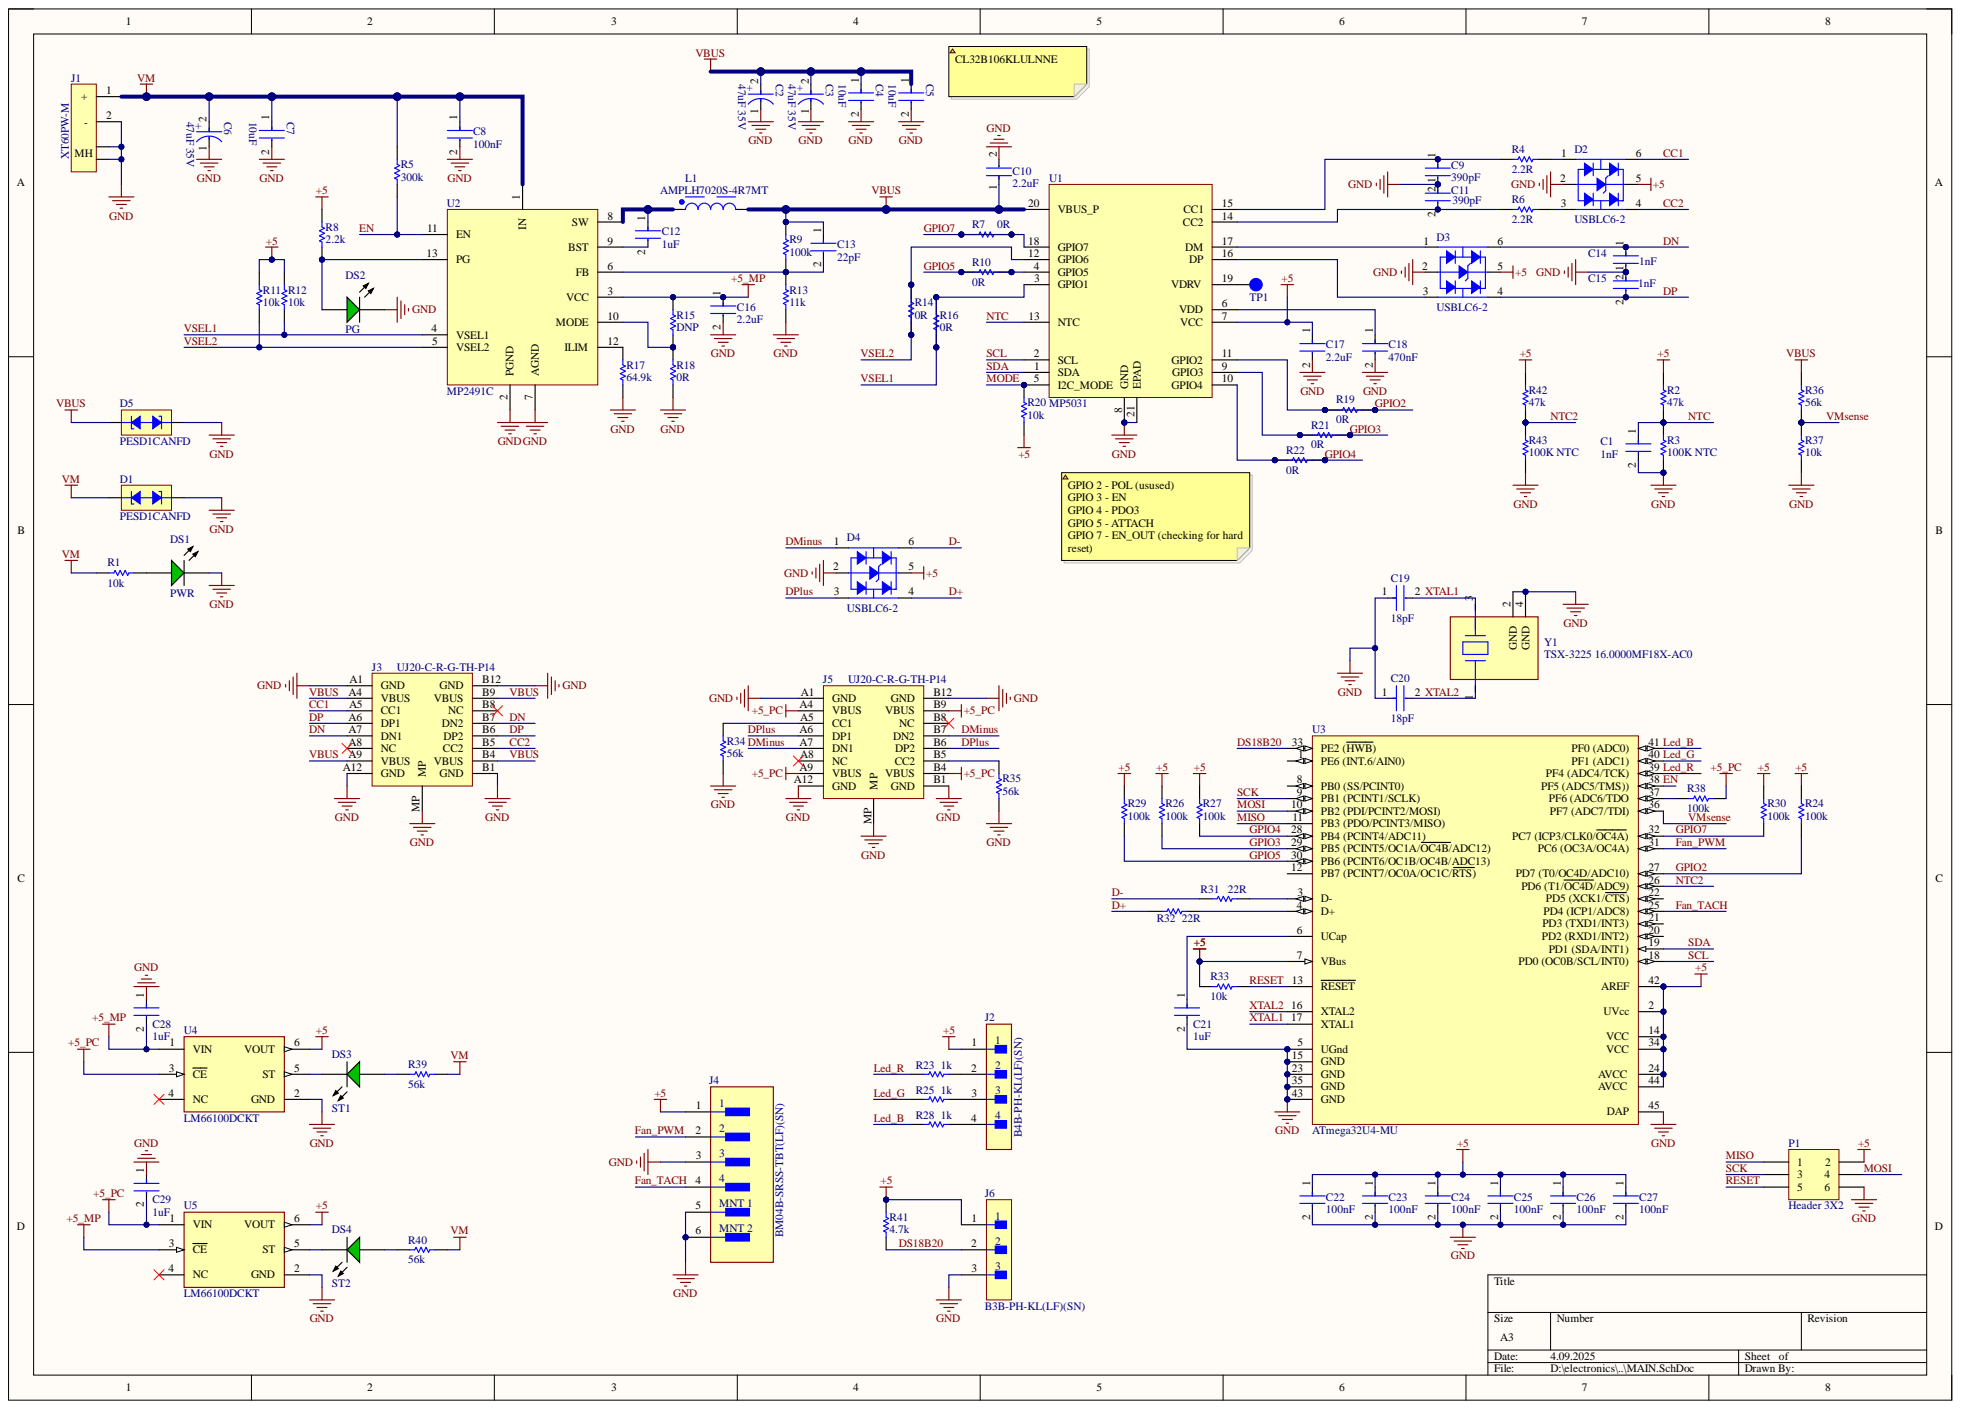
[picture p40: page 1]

R14 | NTC 13

VSEL2

GPIO 2 - POL (usused)
GPIO 3 - EN
GPIO 4 - PDO3
GPIO 5 - ATTACH
GPIO 7 - EN_OUT (checking for hard
reset)

BM04B-SRSS-TBT(LF)(SN)

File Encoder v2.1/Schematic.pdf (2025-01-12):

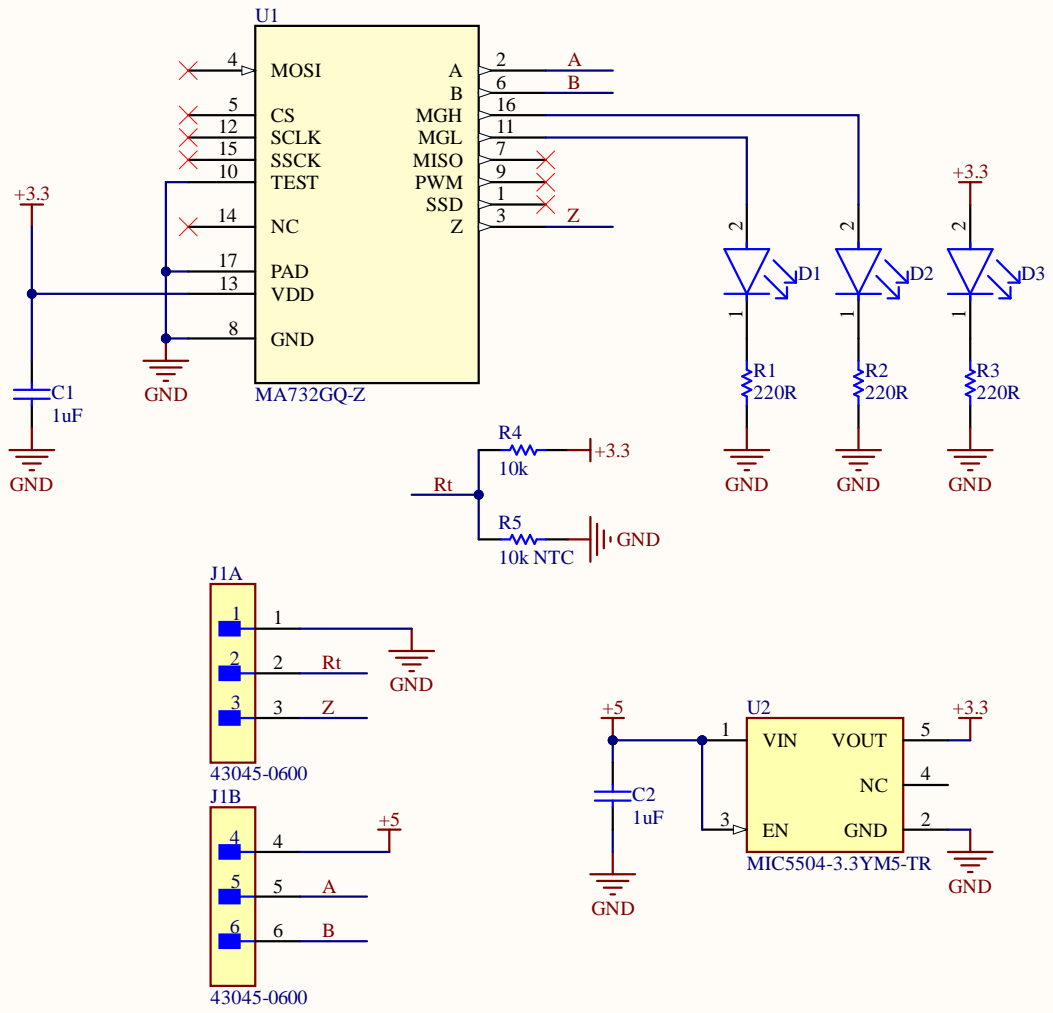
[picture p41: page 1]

PAD 17
VDD 13

GND 8

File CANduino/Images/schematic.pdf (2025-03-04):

# GND 1 2

# GND ¹

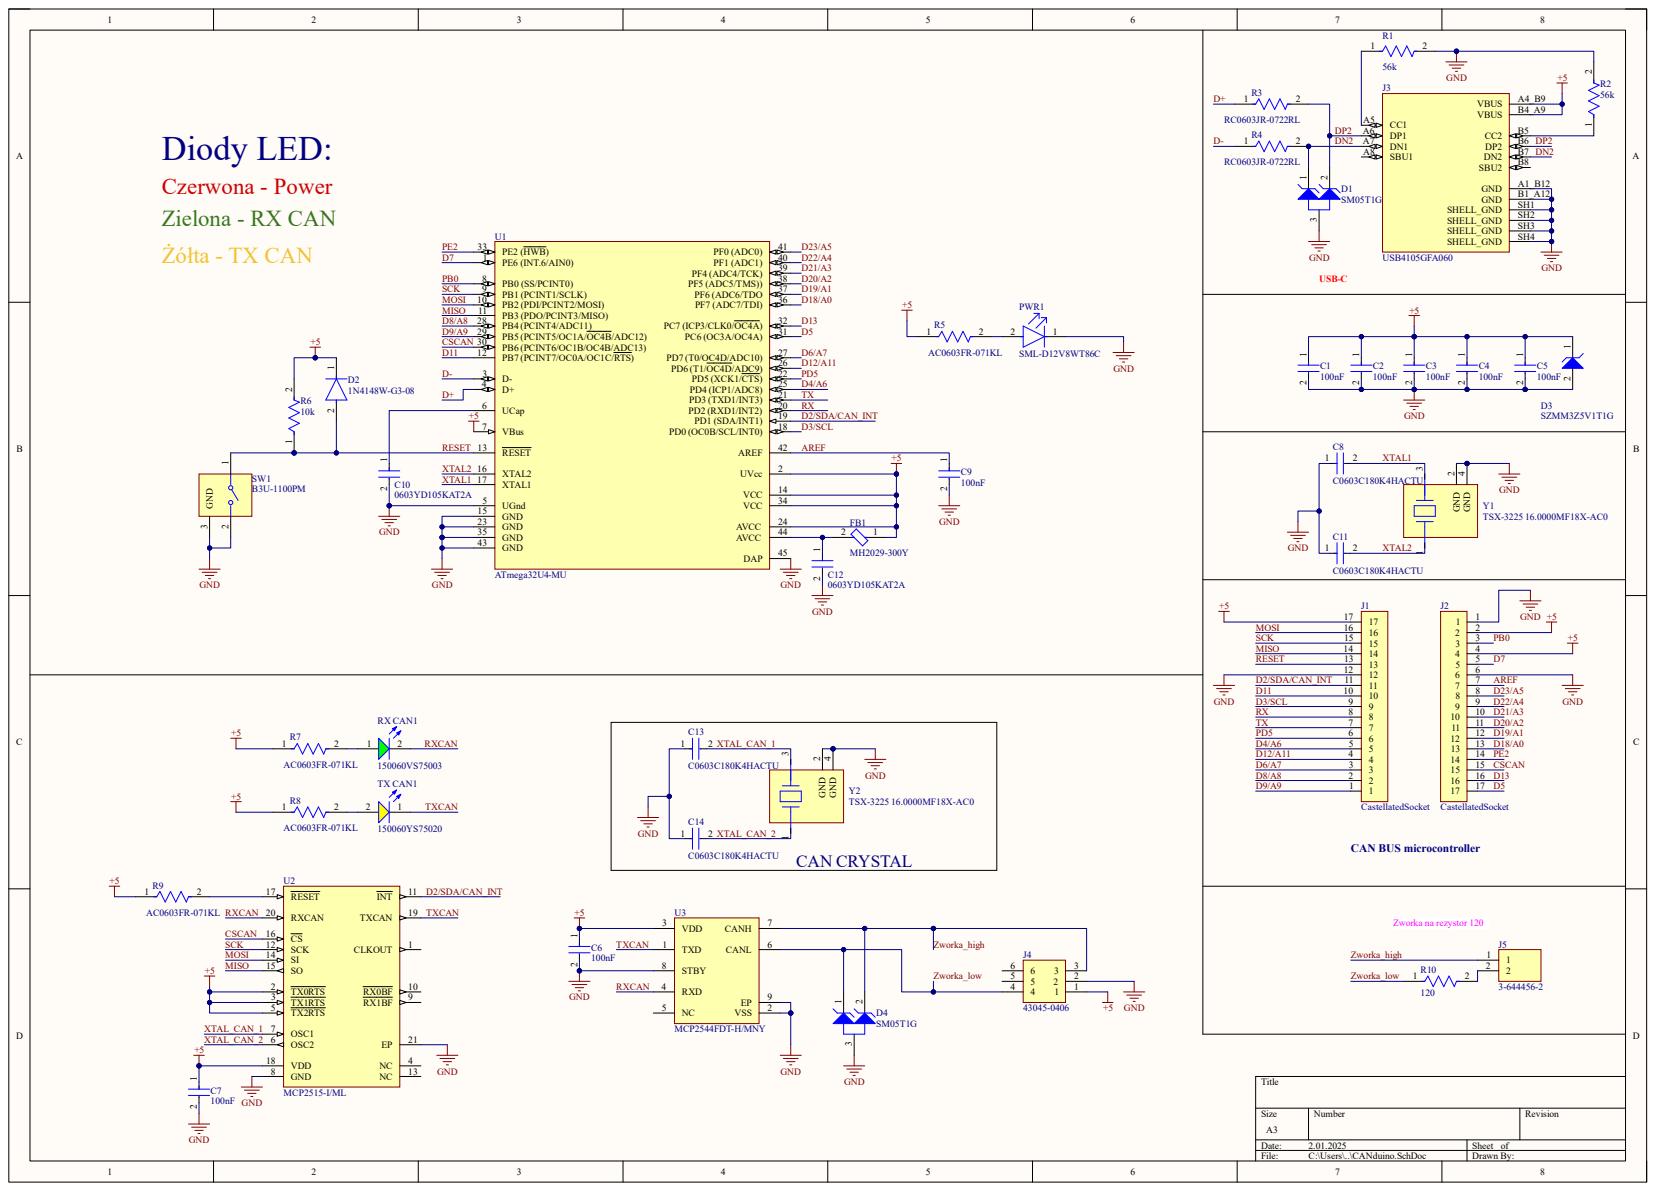
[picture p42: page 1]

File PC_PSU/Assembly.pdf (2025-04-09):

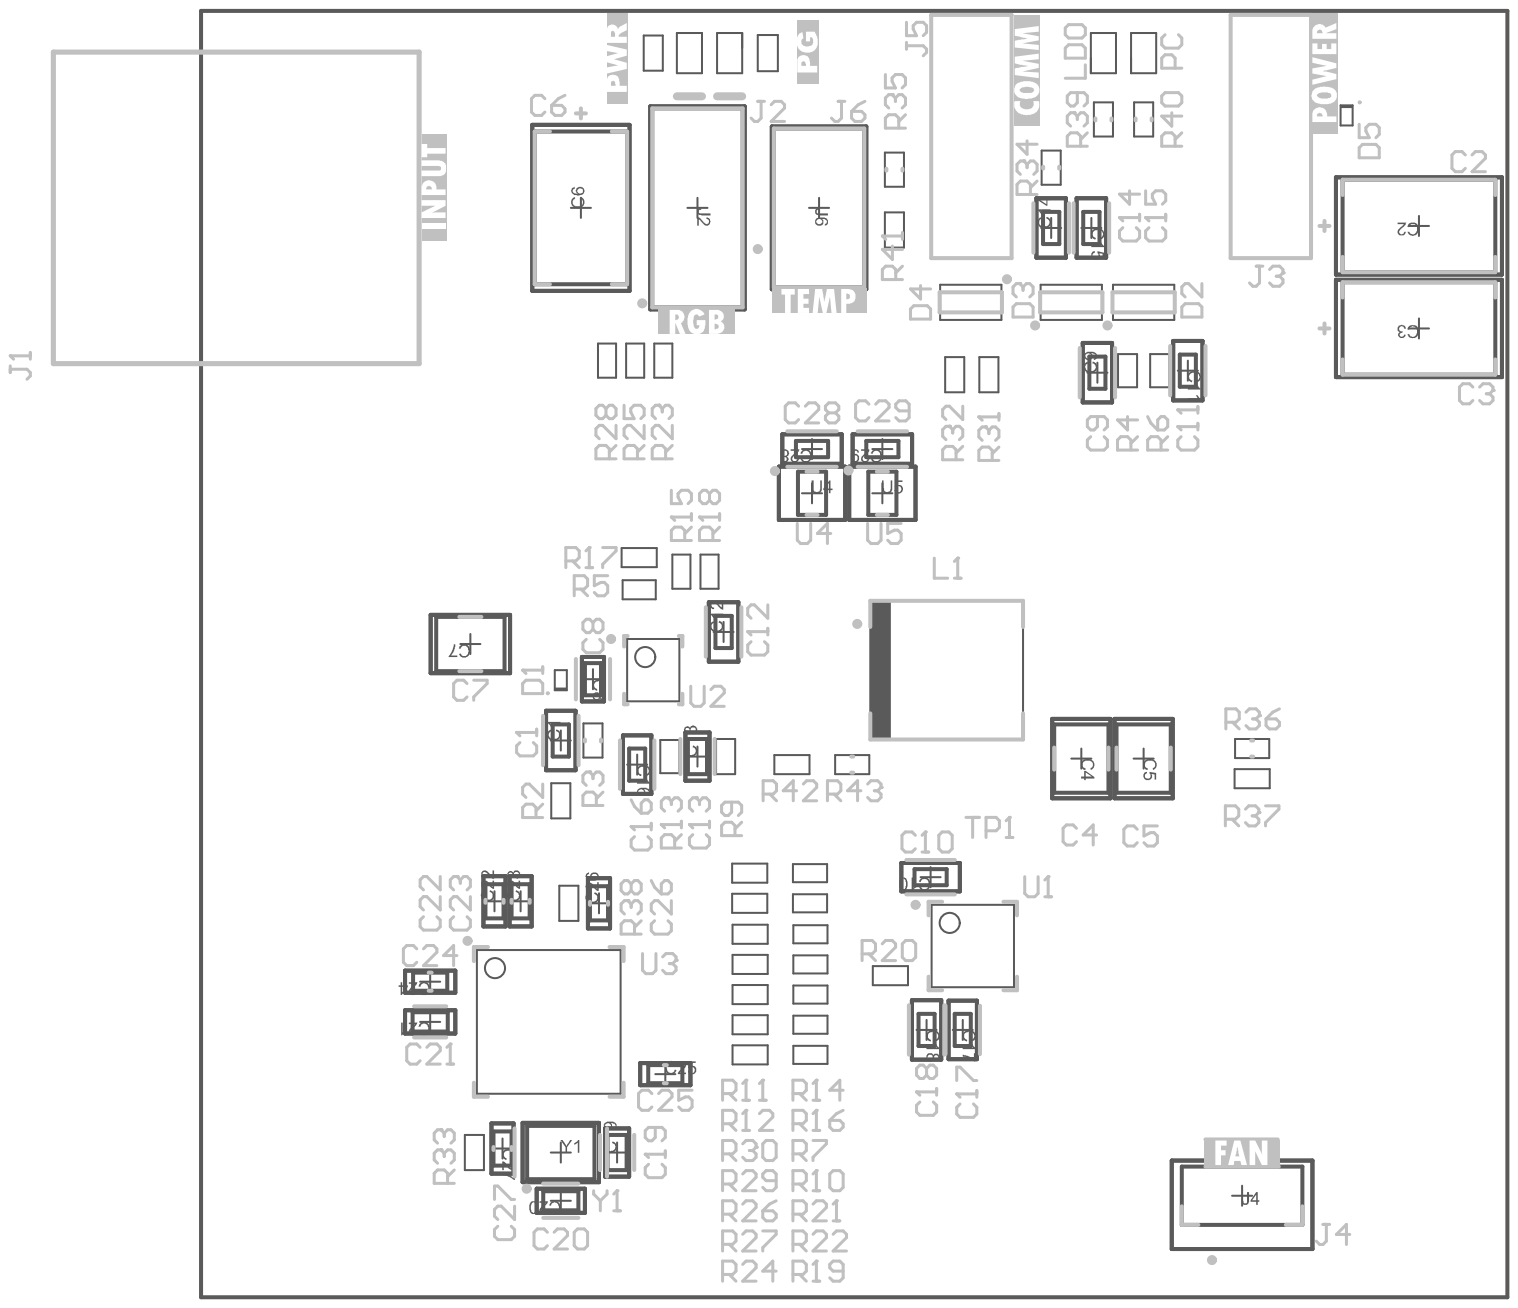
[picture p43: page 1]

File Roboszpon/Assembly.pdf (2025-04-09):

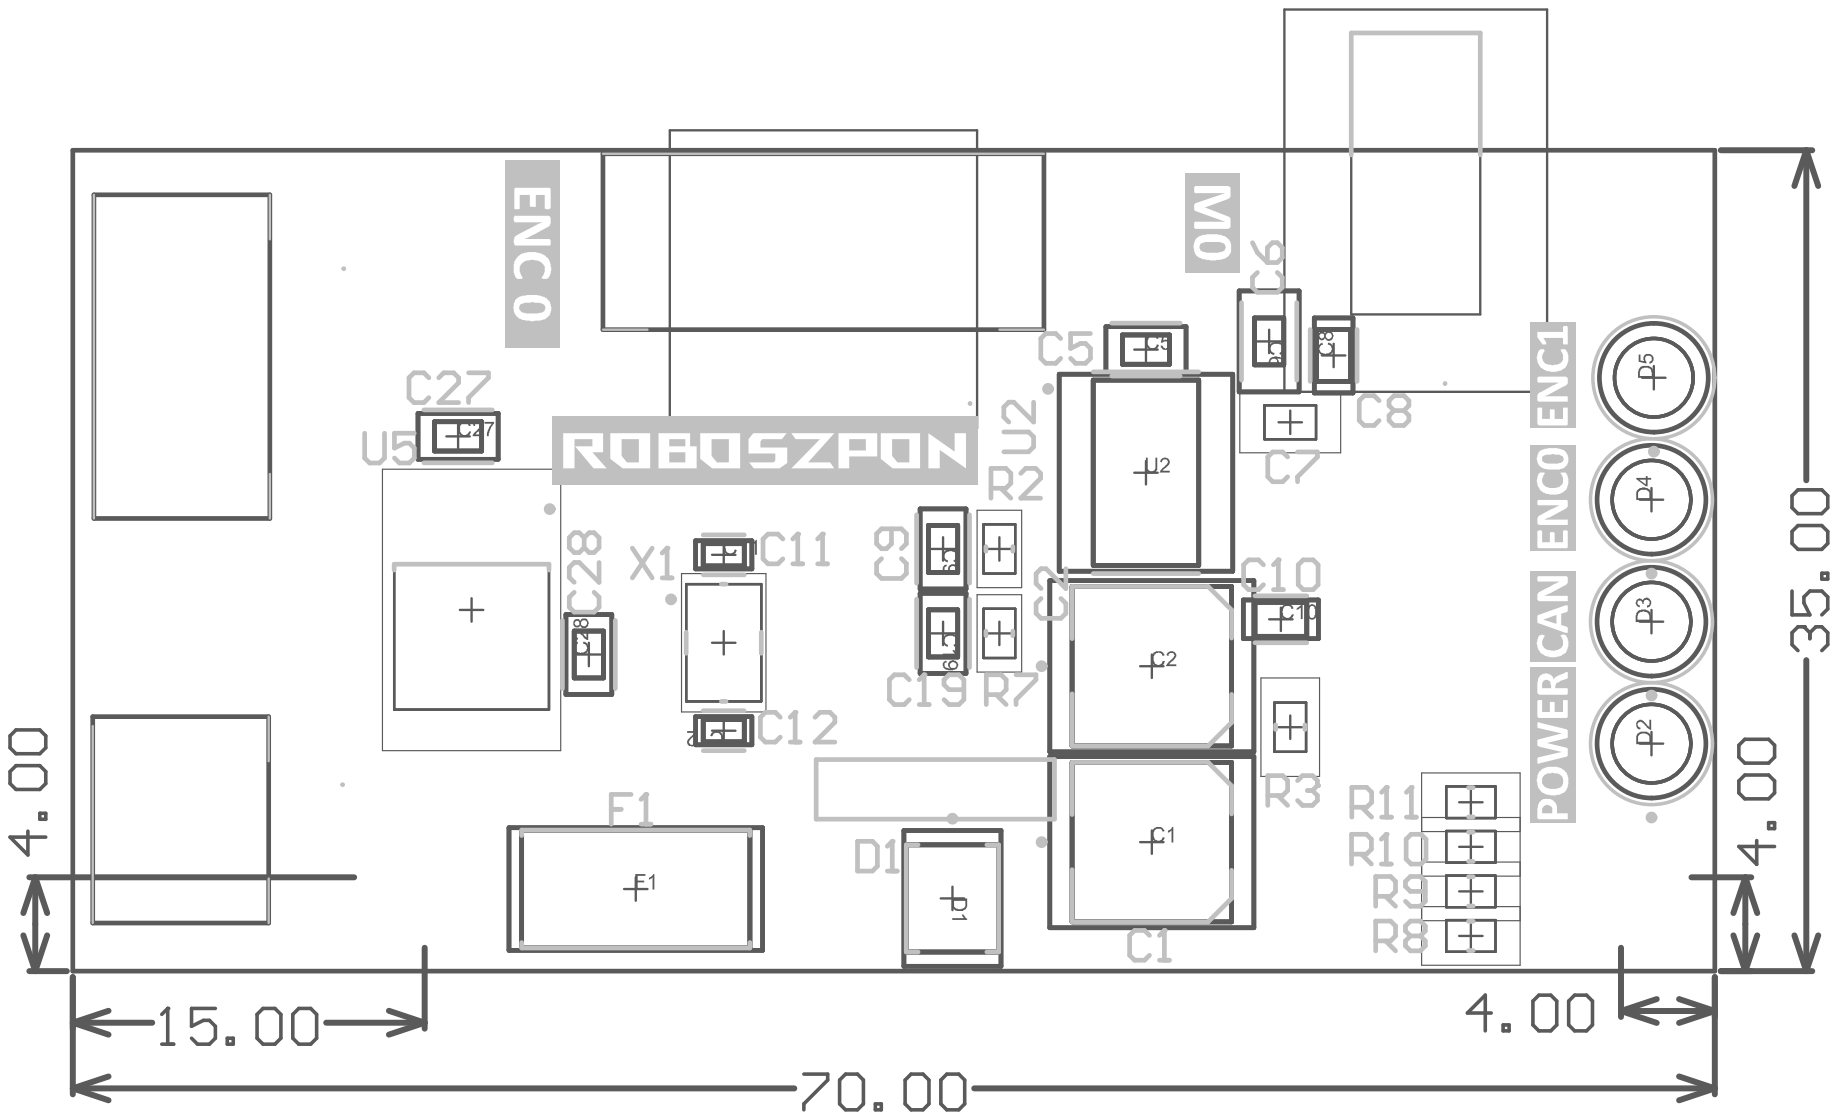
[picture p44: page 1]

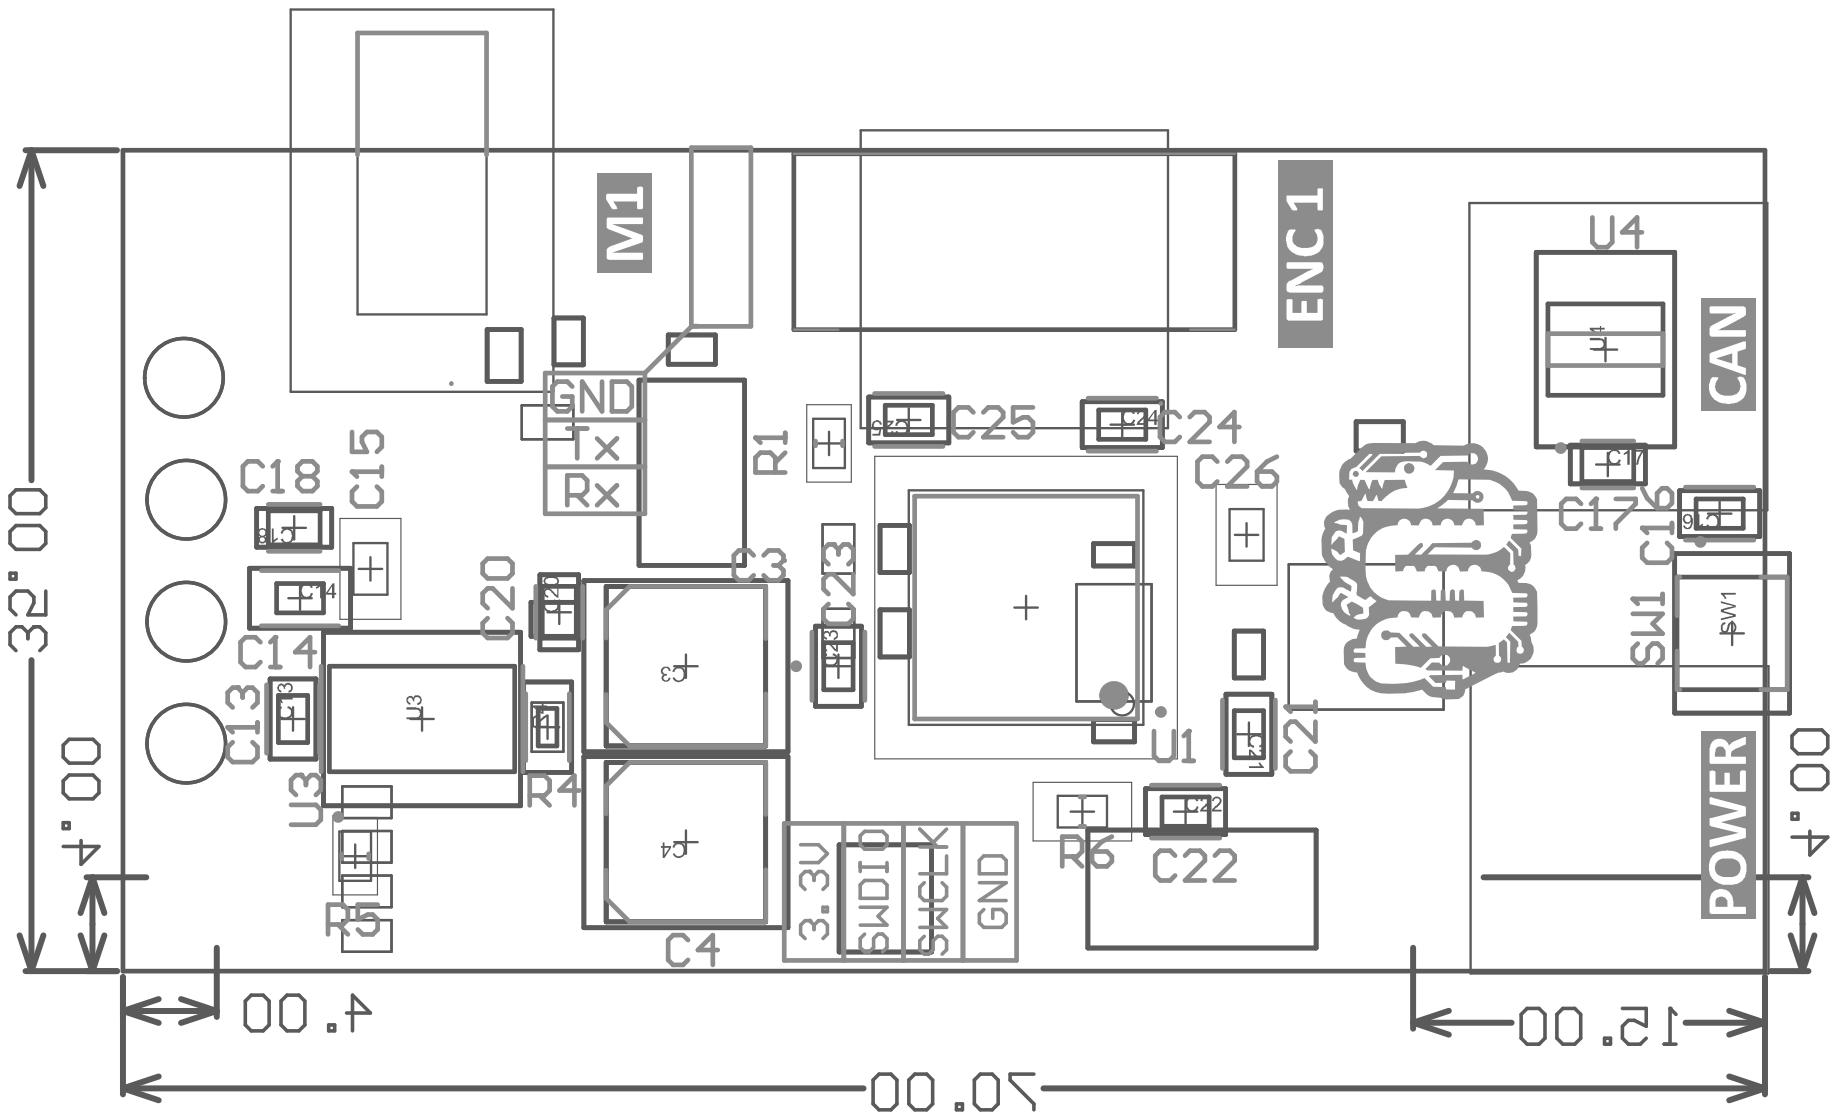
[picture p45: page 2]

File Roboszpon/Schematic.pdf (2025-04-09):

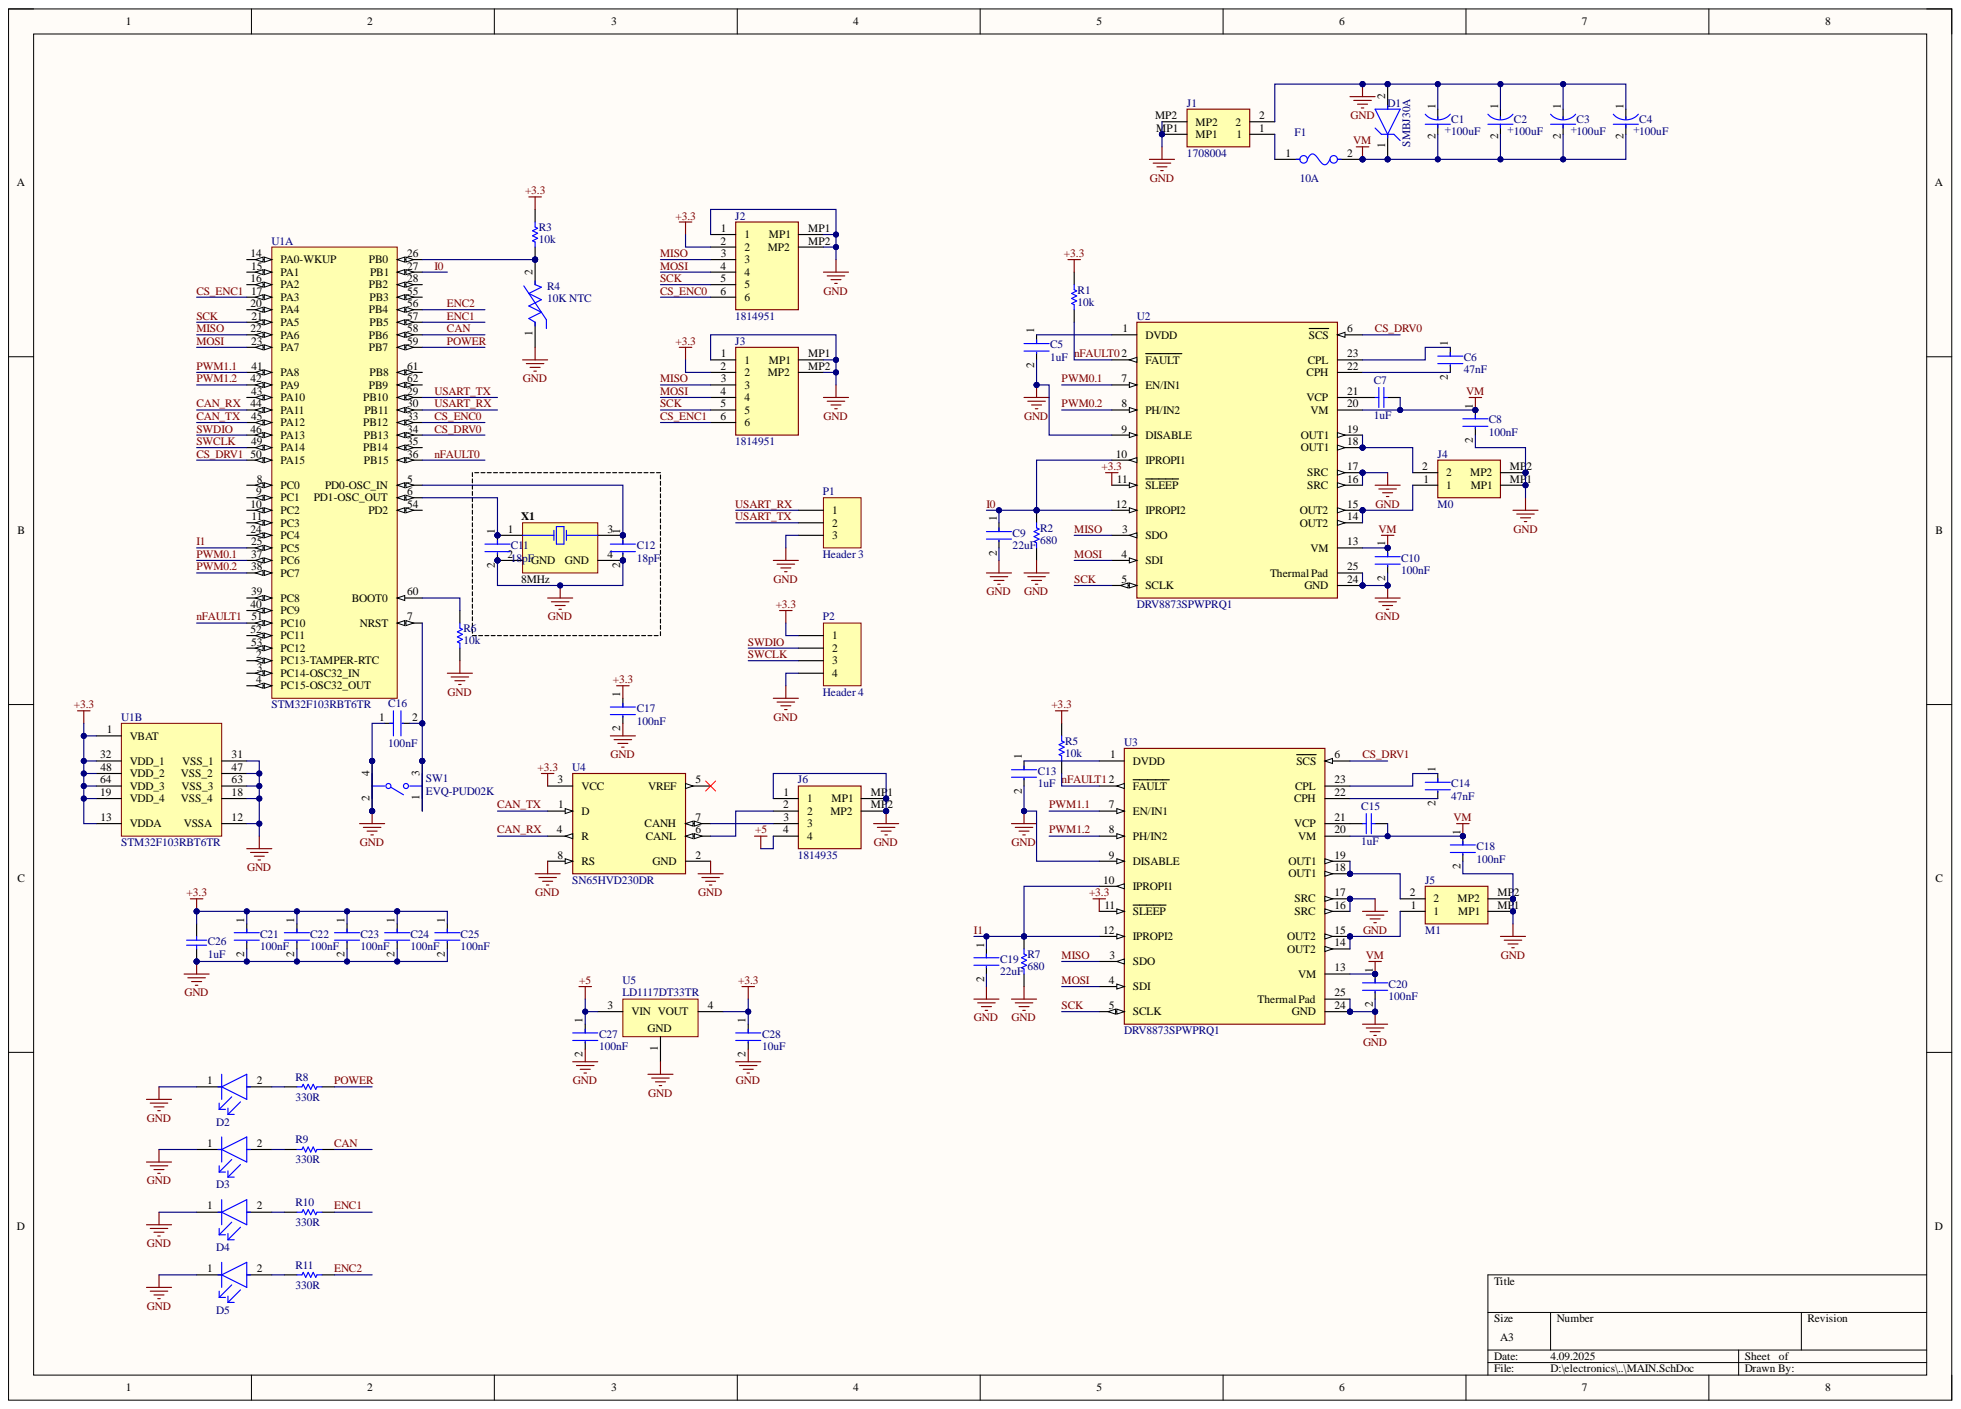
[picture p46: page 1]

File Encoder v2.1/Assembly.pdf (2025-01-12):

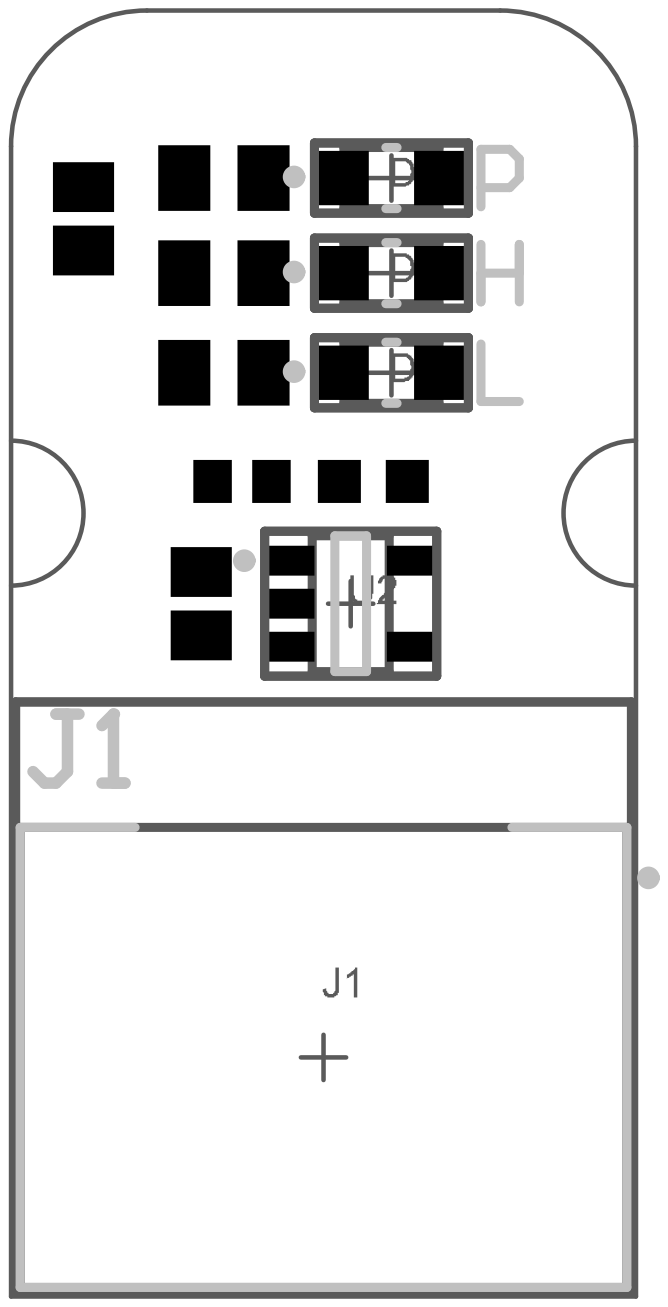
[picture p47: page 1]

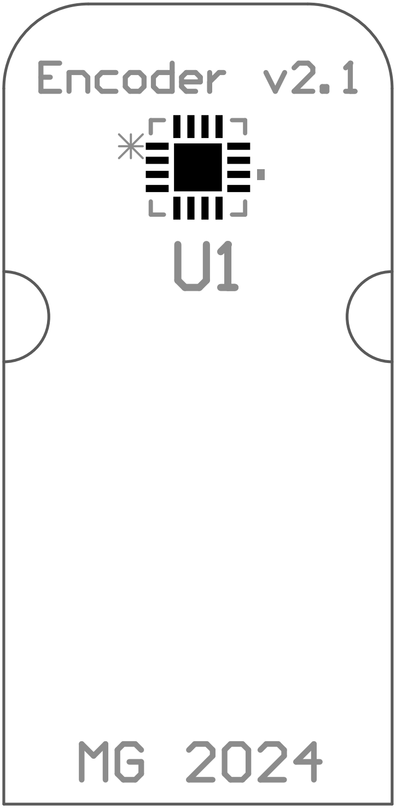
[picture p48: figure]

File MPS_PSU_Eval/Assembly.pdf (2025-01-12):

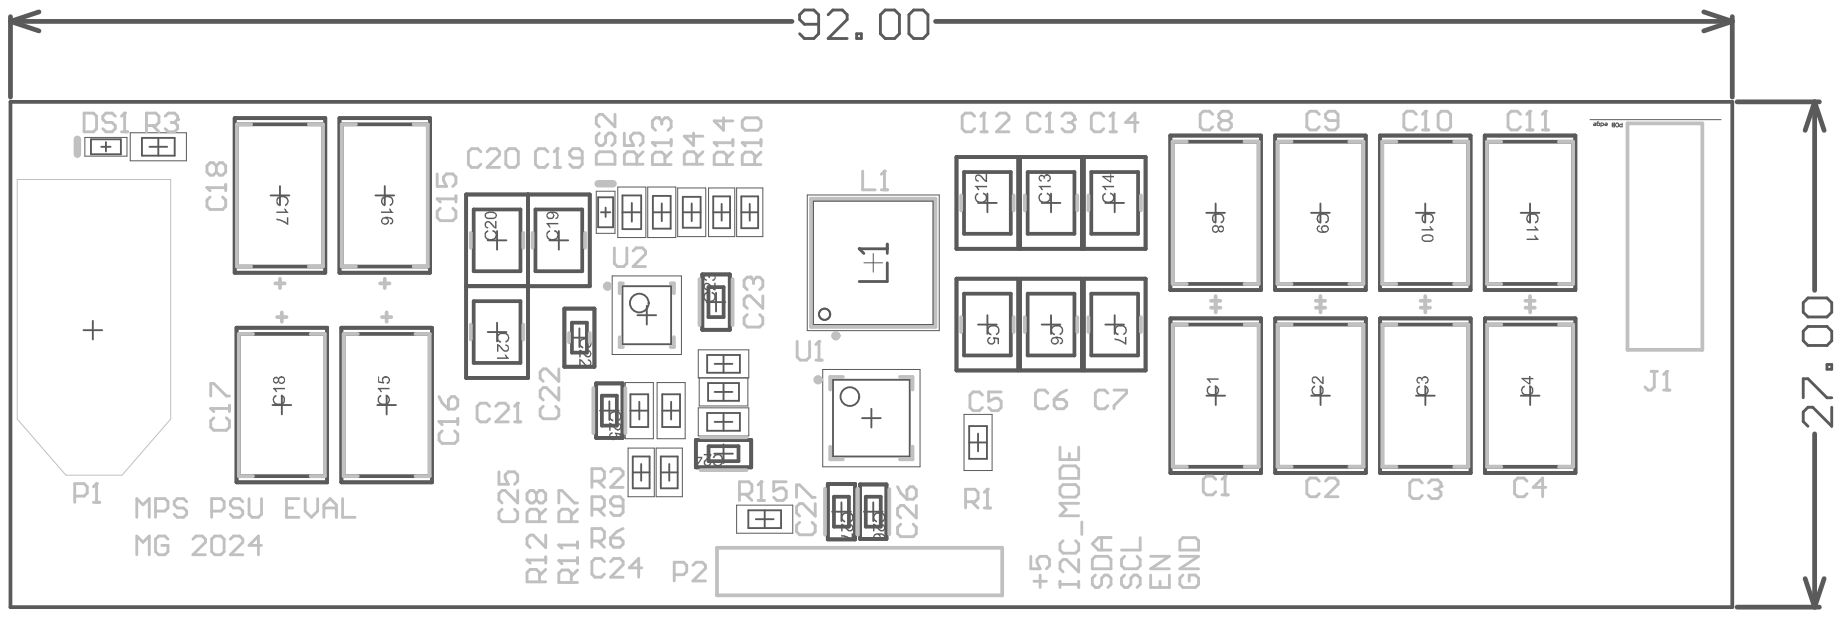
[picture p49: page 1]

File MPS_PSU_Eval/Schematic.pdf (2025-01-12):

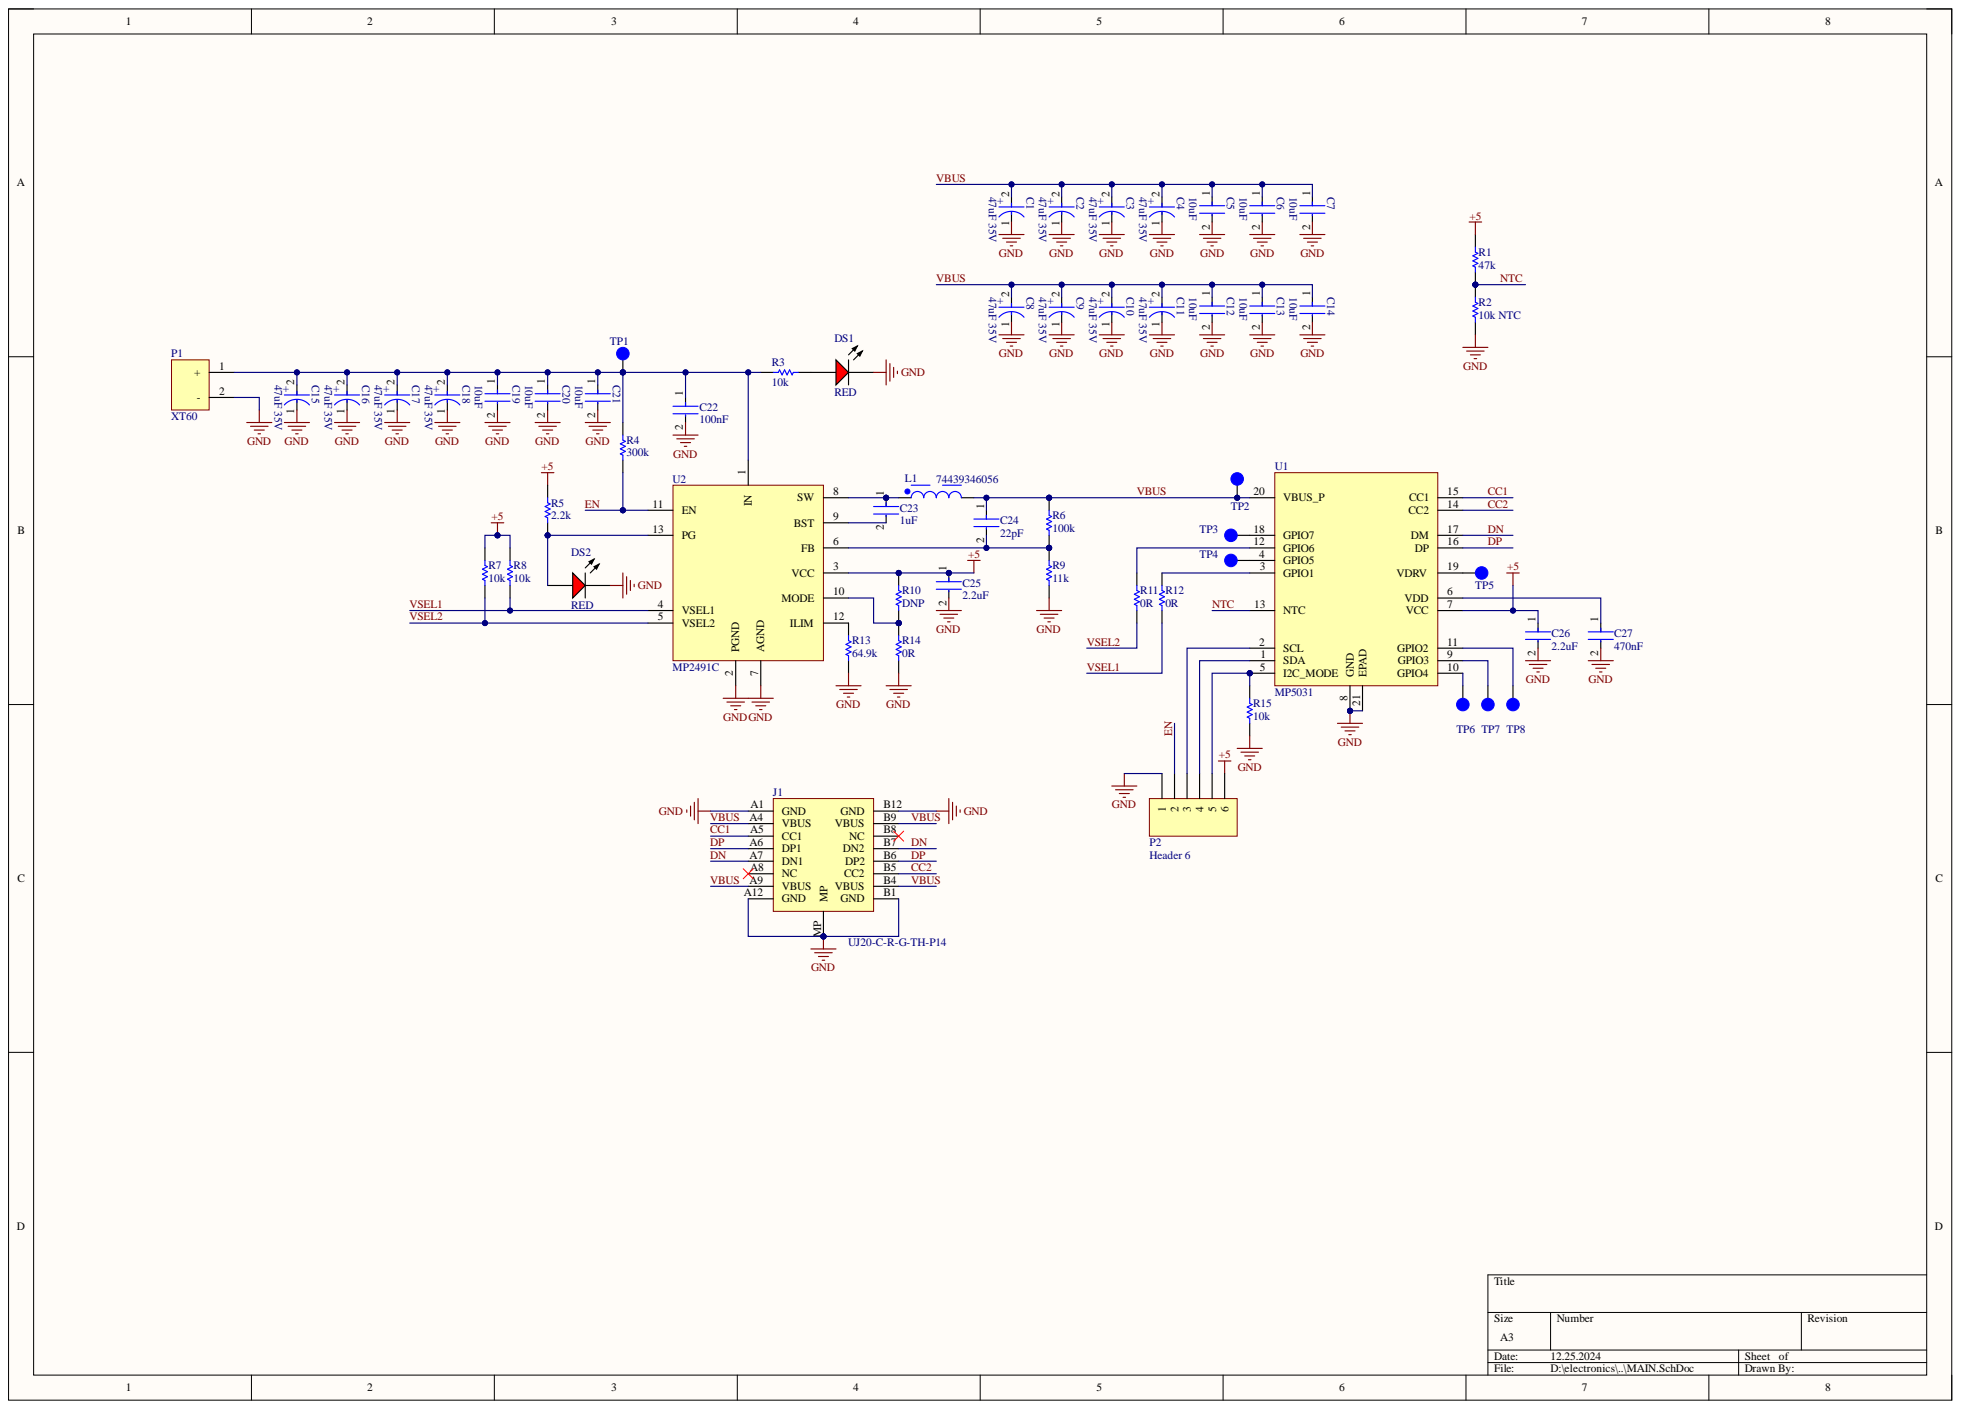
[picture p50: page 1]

VSE L 2

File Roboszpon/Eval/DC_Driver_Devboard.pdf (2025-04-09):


G N | R2 680 MISO D | 3 | | 1 4




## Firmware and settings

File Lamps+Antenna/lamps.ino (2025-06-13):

#include <SPI.h>

const int SPI_CS_PIN = 10;
const int CAN_INT_PIN = 2;

#include <mcp2515.h>
MCP2515 CAN(SPI_CS_PIN); // Set CS pin
struct can_frame canMsg;

#define BLUE_LAMP 2
#define GREEN_LAMP 3
#define YELLOW_LAMP 0
#define RED_LAMP 1
#define BUZZER 4

const uint8_t canId = 0x32;

const long int timeout_time = 3000;
long int latestCommandTime = 0;
bool isTimedOut = true;

const uint32_t canMask = 0b111111 << 5;

void setup() {
    Serial.begin(9600);
    // while(!Serial);

    pinMode(BLUE_LAMP, OUTPUT);
    pinMode(GREEN_LAMP, OUTPUT);
    pinMode(RED_LAMP, OUTPUT);
    pinMode(YELLOW_LAMP, OUTPUT);
    pinMode(BUZZER, OUTPUT);
  
    while (!(CAN.reset() == MCP2515::ERROR_OK
          && CAN.setBitrate(CAN_1000KBPS, MCP_16MHZ) == MCP2515::ERROR_OK
          && CAN.setNormalMode() == MCP2515::ERROR_OK
        )) {

        digitalWrite(RED_LAMP, HIGH);
        digitalWrite(BUZZER, HIGH);
        delay(200);
        digitalWrite(BUZZER, HIGH);
        delay(1000);
        Serial.println("CAN ERROR");
    }

    Serial.println("CAN OK");

    digitalWrite(RED_LAMP, LOW);
    digitalWrite(GREEN_LAMP, LOW);
    digitalWrite(YELLOW_LAMP, LOW);
    digitalWrite(BLUE_LAMP, LOW);
    
    digitalWrite(BUZZER, HIGH);
    delay(100);
    digitalWrite(BUZZER, LOW);
    delay(100);
    digitalWrite(BUZZER, HIGH);
    delay(100);
    digitalWrite(BUZZER, LOW);
}

    
void loop() {
    uint8_t result = CAN.readMessage(&canMsg);
    if (result == MCP2515::ERROR_OK) {
      // Serial.println("Heard msg");
      if ((canMsg.can_id >> 5) == canId) {
          if ((canMsg.can_id & 0b11111) == 0x0) {
              isTimedOut = false;
              latestCommandTime = millis();  
              Serial.println("Got msg");
              digitalWrite(BUZZER, canMsg.data[4]);
              digitalWrite(RED_LAMP, canMsg.data[3]);
              digitalWrite(YELLOW_LAMP, canMsg.data[2]);
              digitalWrite(GREEN_LAMP, canMsg.data[1]);
              digitalWrite(BLUE_LAMP, canMsg.data[0]);
              Serial.print(canMsg.data[4]);
              Serial.print(canMsg.data[3]);
              Serial.print(canMsg.data[2]);
              Serial.print(canMsg.data[1]);
              Serial.print(canMsg.data[0]);
              Serial.println();
          }
      }  
    }
    if (latestCommandTime + timeout_time < millis()) {
      if (!isTimedOut) {
        Serial.println("Timeout");
        digitalWrite(RED_LAMP, 0);
        digitalWrite(YELLOW_LAMP, 0);
        digitalWrite(GREEN_LAMP, 0);
        digitalWrite(BLUE_LAMP, 0);
        digitalWrite(BUZZER, 1);
        delay(500);
        digitalWrite(BUZZER, 0);
      }
      isTimedOut = true;
    }
}

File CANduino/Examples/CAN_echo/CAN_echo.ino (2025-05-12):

#include <SPI.h>
#include <mcp2515.h>

struct can_frame canMsg;
MCP2515 mcp2515(10);


void setup() {
  Serial.begin(115200);
  
  mcp2515.reset();
  mcp2515.setBitrate(CAN_1000KBPS, MCP_16MHZ);
  mcp2515.setNormalMode();
  
  Serial.println("------- CAN Read ----------");
  Serial.println("ID  DLC   DATA");
}

void loop() {
  if (mcp2515.readMessage(&canMsg) == MCP2515::ERROR_OK) {
    Serial.print(canMsg.can_id, HEX); // print ID
    Serial.print(" "); 
    Serial.print(canMsg.can_dlc, HEX); // print DLC
    Serial.print(" ");
    
    for (int i = 0; i<canMsg.can_dlc; i++)  {  // print the data
      Serial.print(canMsg.data[i],HEX);
      Serial.print(" ");
    }

    Serial.println();      
  }
}

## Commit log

2023-03-15 first libraries, and sajens pcb
    [DC motors drivers.PcbLib, DC motors drivers.SchLib, SCIENCE.SchDoc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]
2024-03-23 Added first magnetic encoder files
    [Encoder.PrjPcb, Encoder_3D_model.step, PCB1.PcbDoc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]
2024-07-07 Added new small encoder CAD files
    [6044691488.SLDPRT, 61200821621.SLDASM, 61200821621.SLDPRT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]
2024-07-07 Changing wrong files to correct one
    [6044691488.SLDPRT, 61200821621.SLDASM, 61200821621.SLDPRT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]
2024-10-14 Renamed encoder v1 source files
    [Encoder.PcbDoc, MAIN.SchDoc]
2024-10-14 -Added readme -Added Roboszpon -Moved old files
    [DC motors drivers.PcbLib, DC motors drivers.SchLib, DC_motor_driver.PrjPcb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]
2024-10-15 Test commit
    [MAIN.SchDoc]
2024-10-16 Updated component comments
    [MAIN.SchDoc]
2024-10-16 Updated placement
    [MAIN.SchDoc]
2024-11-10 Repository cleanup and file management
    [CANdruino.PcbDoc, CANdruino.PrjPcb, CANdruino.SchDoc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]
2024-11-10 Ustawienie pinoutu zgodnie ze standardem Arduino Micro
    [CANdruino.SchDoc]
2024-11-10 Poprawienie literówki w nazwie
    [CANdruino.PcbDoc, CANdruino.SchDoc, CANduino.PcbDoc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]
2024-11-10 Przypisanie schematu i pcb do projektu
    [CANduino.PrjPcb]
2024-11-10 Zmiana kondensatorów C1-C5
    [CANduino.PcbDoc, CANduino.SchDoc]
2024-11-15 Zmiana transceivera CAN
    [CANduino.PcbDoc, CANduino.SchDoc]
2024-11-15 Dodanie PWR LED
    [CANduino.PcbDoc, CANduino.SchDoc]
2024-11-16 Zmieniono CAN controller na MCP2515
    [CANduino.PcbDoc, CANduino.PrjPcb, CANduino.SchDoc]
2024-11-16 Dodanie diody LED sygnalizującej komunikację z CANem
    [CANduino.PcbDoc, CANduino.SchDoc]
2024-11-16 Zmieniono rulsy
    [CANduino.PcbDoc]
2024-11-17 Zmiana układu pcb
    [CANduino.PcbDoc, CANduino.SchDoc]
2024-11-17 Pierwsza wersja ścieżek
    [CANduino.PcbDoc, CANduino.SchDoc]
2024-11-18 Zmiana ścieżek i diody komunikacji CAN
    [CANduino.PcbDoc, CANduino.SchDoc]
2024-11-18 Nowy plan ścieżek
    [CANduino.PcbDoc, CANduino.SchDoc]
2024-11-18 Test altium comment
    [CANduino.PcbDoc]
2024-11-18 Zmiany na schemacie
    [CANduino.PcbDoc, CANduino.SchDoc]
2024-11-18 Nowe ułożenie PCB
    [CANduino.PcbDoc, CANduino.SchDoc]
2024-11-19 Nowe ścieżki, nowy design
    [CANduino.PcbDoc, CANduino.SchDoc]
2024-11-22 Zmiana wymiarów płytki
    [CANduino.PcbDoc, CANduino.SchDoc]
2024-11-22 Zmiana wymiarów płytki, dodanie linii zasilania
    [CANduino.PcbDoc, CANduino.PrjPcb, CANduino.SchDoc]
2024-11-23 Zmiana diody D5 - brak w sklepie
    [CANduino.PcbDoc, CANduino.SchDoc]
2024-11-25 Initial commit, libraries added
    [MAIN.SchDoc, MPS.PcbLib, MPS.SchLib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]
2024-11-26 Schematic done
    [MAIN.SchDoc, MPS.PcbLib, MPS.SchLib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]
2024-11-26 Added EN to external pin
    [MAIN.SchDoc]
2024-12-01 PCB done
    [MAIN.SchDoc, MPS.PcbLib, MPS.SchLib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]
2024-12-02 Dodano protorym castellated hole
    [CANduino.PcbDoc, CANduino.SchDoc]
2024-12-02 Dodano castellated holes
    [CANduino.PcbDoc, CANduino.SchDoc]
2024-12-02 Dodanie modeli 3D
    [43045-0400.stp, CANduino.PcbDoc, CANduino.SchDoc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]
2024-12-03 Small changes
    [CANduino.PcbDoc, CANduino.SchDoc]
2024-12-10 Dodanie poligonu GND na warstwie 1 i 4
    [CANduino.PcbDoc]
2024-12-10 Dodanie nowego micro-fita
    [CANduino.PcbDoc, CANduino.PrjPcb, CANduino.SchDoc]
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2024-12-16 Tidying up Changed castellated holes
    [CANduino.PcbDoc, CANduino.SchDoc]
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2024-12-24 Replace all to 0603
    [CANduino.PcbDoc, CANduino.SchDoc]
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2024-12-26 Improved track/track clearance
    [CANduino.PcbDoc]
2024-12-26 Reverted edge connector
    [CANduino.PcbDoc]
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2025-01-05 Zmiana kondensatora C12 na ten sam co C10
    [CANduino.PcbDoc, CANduino.PrjPcb, CANduino.SchDoc]
2025-01-05 Zmieniono rezystory R7 R8 R9 na takie same co R5
    [CANduino.PcbDoc, CANduino.SchDoc]
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2025-01-06 Added graphic, geenrated gerbers
    [CANduino.PcbDoc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]
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2025-01-07 Updated gerbers for production
    [MPS_PSU_Eval.PcbDoc, MPS_PSU_Eval.PrjPcb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]
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2025-01-12 Updated documentation and readme
    [Encoder_v2.1.PcbDoc, Encoder_v2.1.PrjPcb, Encoder_v2.1_3D_model.step]
2025-01-12 Removed missing files (encoder v2.1)
    [Encoder_v2.1.PrjPcb]
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2025-02-24 Fixed footprint
    [CANduino.SchLib]
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2025-03-04 Changed color code of encoders
    [Encoder_v2.1.PcbDoc, Encoder_v2.PcbDoc]
2025-03-05 Changed components for Digikey
    [lamps+antenna.SchDoc]
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2025-03-05 Added RJ45 3D model
    [2501551-6.stp]
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2025-03-07 Corrected impedance in PoE
    [lamps+antenna.PrjPcb]
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2025-03-09 Initial commit, added inductor lib
    [MAIN.SchDoc, MPS_PSU_Eval.PcbDoc, PC_PSU.PcbDoc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]
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2025-03-11 Changed board thickness and footprint
    [CANduino.PcbDoc, CANduino.PrjPcb, CANduino.SchDoc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]
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2025-03-12 Updated pictures and CANduinolib
    [CANduino.PcbDoc, CANduino.PrjPcb, CANduino.SchLib]
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2025-03-13 Lib update, cooler 3D model added
    [MAIN.SchDoc, PC_PSU.PcbDoc, PC_PSU.PrjPcb]
2025-03-14 Changed resistors to 0805
    [lamps+antenna.SchDoc]
2025-03-18 Changed capasitors to 0805
    [lamps+antenna.SchDoc]
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2025-03-30 Schematic done, basic placement
    [MAIN.SchDoc]
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2025-04-03 Added new CANduino footprint
    [lamps+antenna.SchDoc]
2025-04-04 Schematic cleaniup Overlay layer done
    [MAIN.SchDoc, PC_PSU.PrjPcb]
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2025-04-05 Created pcb for communication with cameras
    [cameras.PcbDoc, cameras.PrjPcb, cameras.SchDoc]
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2025-04-08 Fabrication and 3D model output
    [PC_PSU.PrjPcb]
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2025-04-09 Added raw source for roboszpon eval
    [DC_Driver_Devboard.PrjPcb, PCB1.PcbDoc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]
2025-04-09 Generated x2 gerbers files
    [cameras.PrjPcb]
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

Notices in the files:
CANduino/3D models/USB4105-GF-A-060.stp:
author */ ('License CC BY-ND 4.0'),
